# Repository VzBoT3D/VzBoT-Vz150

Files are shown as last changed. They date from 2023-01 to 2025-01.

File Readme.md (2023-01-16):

# VzBoT  <a href='https://ko-fi.com/vez3d' target='_blank'>Buy Me a Coffee at ko-fi.com</a> 

Discord Invite (https://discord.gg/KWZWvCMxCq)

The Vz-150 is a smaller sized VzBoT with a bed print size of 150 x 150 x 125 mm and an optional AWD setup, for which we named the Kinematics "QuadXY" 

The AWD version is still very experimental but is proving to be great for high speed printing without loss of quality!

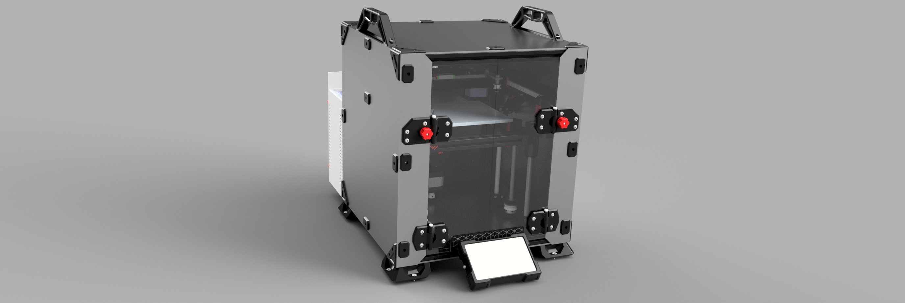
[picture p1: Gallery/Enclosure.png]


This project is licensed as


https://creativecommons.org/licenses/by-nc/4.0/

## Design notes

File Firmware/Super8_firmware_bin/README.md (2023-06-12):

## Pre-compile firmware for the 3 different Super8 versions: 

Instructions:

1. Check your board to make sure you are flashing the right versions. There are 3 versions for now.
    - Super8 standard v1.x (STM32F407 @ 168mhz)
    - Super8 Pro (first edition with STM32H743 chip @ 480mhz)
    - Super8 Pro (latest edition with STM32H723 chip @ 525mhz)

2. Download the according firmware file and rename it to firmware.bin
3. Plate the firmware.bin file on the Super8 Pro SDCARD
4. power on 



Super8 V1.x Standard (STM32F407 @ 168mhz):
 

Super8 Pro (first edition with STM32H743 chip @ 480mhz):
 

Super8 Pro (latest edition with STM32H723 chip @ 525mhz):


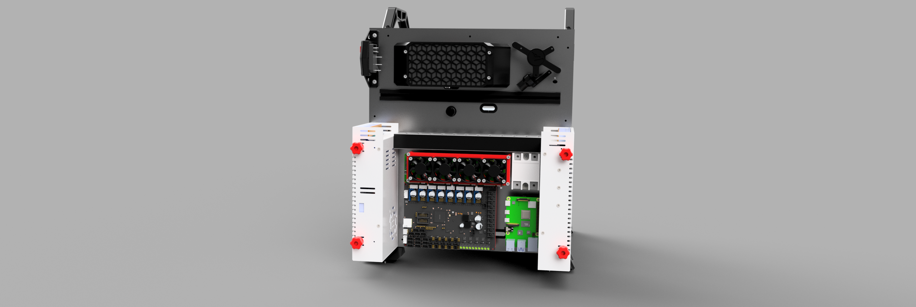
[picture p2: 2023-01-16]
Gallery/Electronics.png

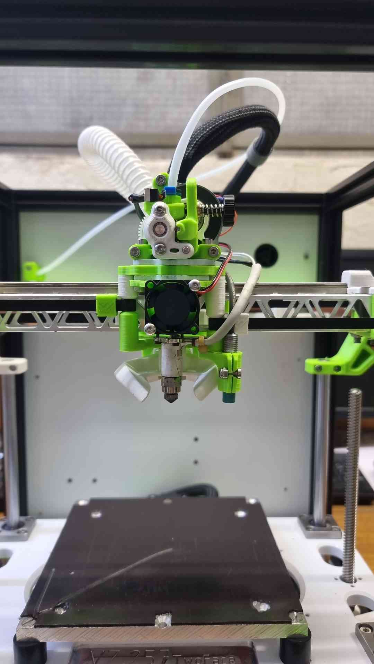
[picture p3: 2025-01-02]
Gallery/IMG-20240227-WA0013.jpg

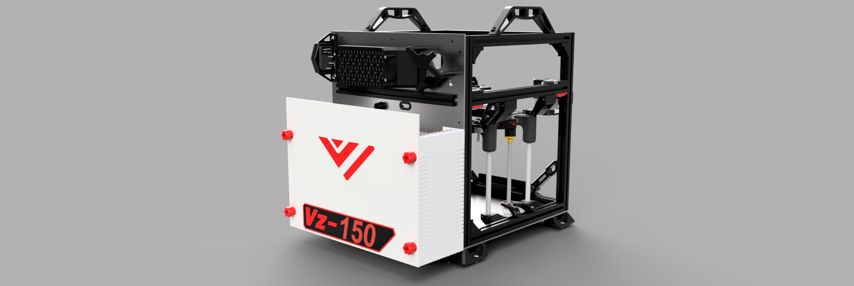
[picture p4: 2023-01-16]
Gallery/Backside.png

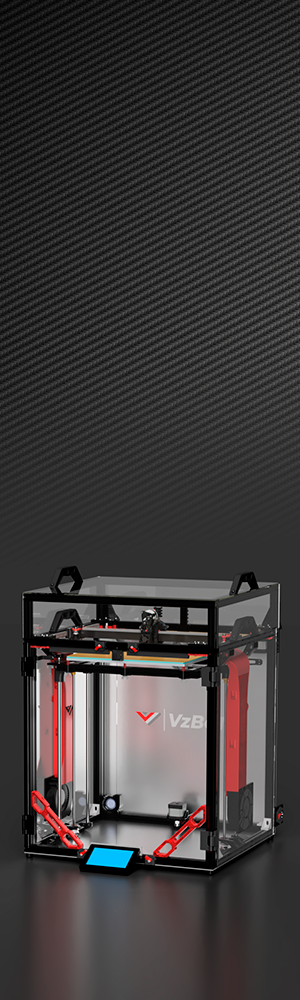
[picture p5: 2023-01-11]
mainsail theme/Theme1/sidebar-background.png

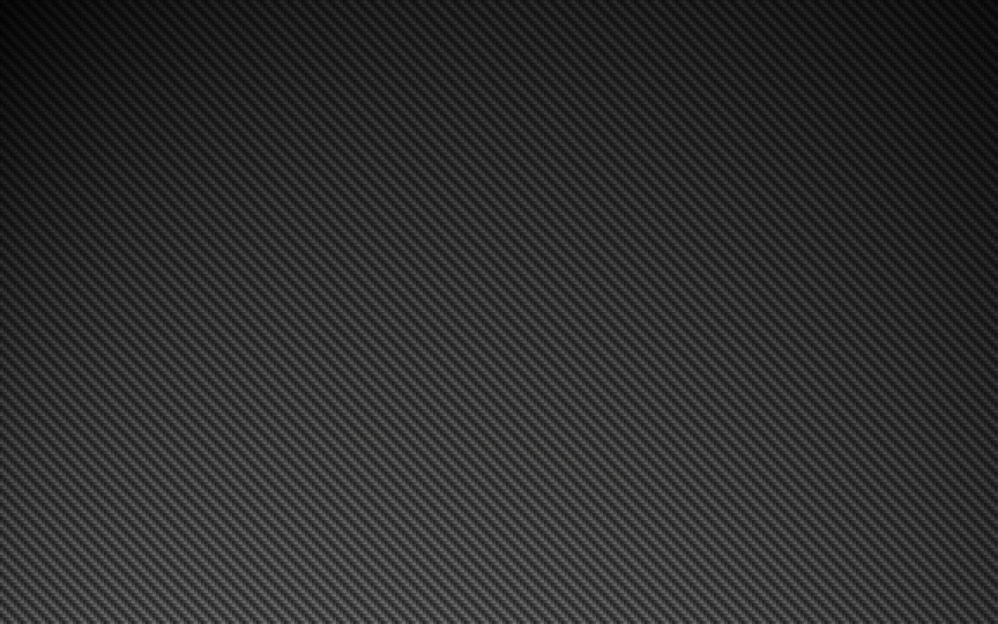
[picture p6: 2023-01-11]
mainsail theme/Theme1/main-background.png

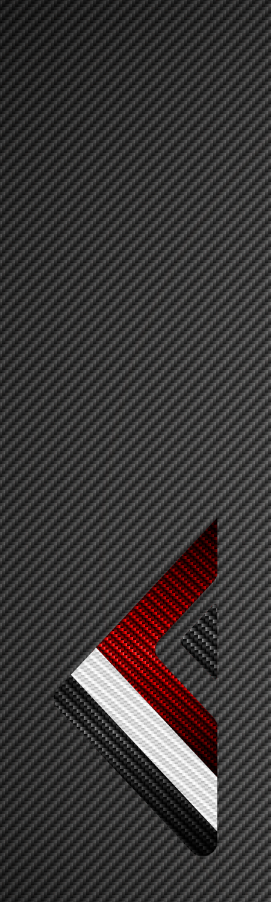
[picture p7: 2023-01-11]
mainsail theme/Theme2/sidebar-background.png

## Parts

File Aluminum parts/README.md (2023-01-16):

# Aluminium parts 

## As available at https://f3d-racing-fdm.myshopify.com/collections/vzbot-vz235

Download the full manual, which includes BOM & print list for all aluminum goodness, above or download the per product manual

Vz150 uses the Aluminium AWD and 2WD mounts from the Vz235. this also includes the Front motor mounts and aluminium Y mounts.

For the Aluminium Y mounts a extra adapter piece is needed found here: [adapter](https://github.com/VzBoT3D/VzBoT-Vz150/tree/main/Aluminum%20parts/Y%20gantry%20adapter)

AWD gantry4

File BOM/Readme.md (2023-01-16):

Work in Progress. Bolts section not fully up to date.

[BOM](https://docs.google.com/spreadsheets/d/1rttVg8Ff3fgsPedlMMFiKo6rYP4tSjWZuqir-3zcSh8/edit?usp=sharing)

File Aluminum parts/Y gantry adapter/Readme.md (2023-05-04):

The adapters can be bought here [MGN9C Adapter](https://s.click.aliexpress.com/e/_DBB861L)

Or you can make them yourself with the provided file.
This part is best when made in aluminium.

BOM:

4x M3x8 Socket Head.                    For mounting the Aluminium Y parts to the adapter.
4x M3x4 Button Head or Ultra Flat head. For mounting the Adapter to the MGN9C carriage.

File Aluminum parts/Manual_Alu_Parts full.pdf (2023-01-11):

## About

This manual is intended for the aluminum parts for VZ235 as sold by F3D-Racing and Mellow. The aluminum parts are interchangeable with the printed parts, some additional hardware is required when purchasing the motor mounts and idler mounts. Furthermore some printed parts are required in order to mount your new sexy parts!

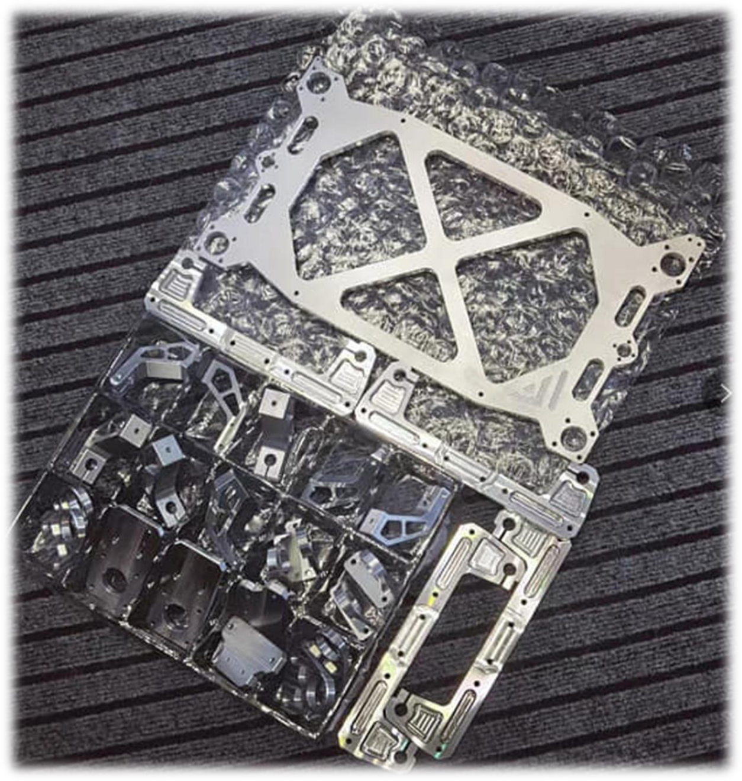
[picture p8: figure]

*Disclaimer: VzBoT is an opensource passion project, this manual is not definitive, and we try to make it as polished as possible. Fortunately, we all make errors so use common sense when following this guide.

## Print settings:

We recommend printing all parts in ABS, ASA or similar material to be able to withstand the high heat environment in the printer enclosure.

Print settings should always be tuned for your own material and tested for decent strength and layer adhesion.

We recommend the following settings:

For non-moving parts:

Layer height: 0.2mm

Layer with: 0.4 to 0.6 mm

Number of walls: 4

Infill percentage: 40 to 50 %

Top/bottom layers: 5

For moving parts:

Layer height: 0.2mm

Layer with: 0.4 to 0.6 mm

Number of walls: 4

Infill percentage: 30 to 40 % depending on your material

Top/bottom layers: 5

## 1. Gantry

Overview:

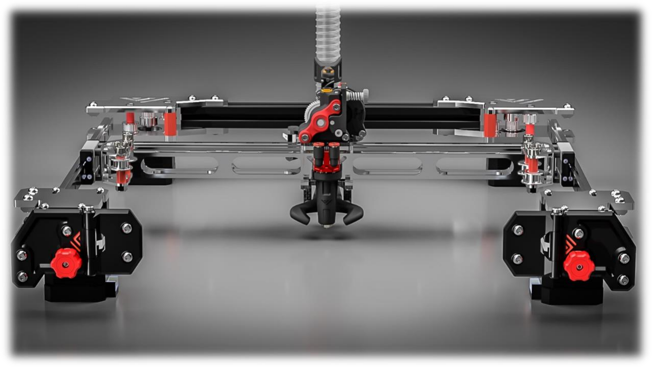
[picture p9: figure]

The Gantry is configurable for an AWD version and a 2WD version. The only difference between the two configurations is the rear idler mounts. On AWD they have an additional Nema 17 integrated in the design.

1.1 Motor mounts + integrated hinges

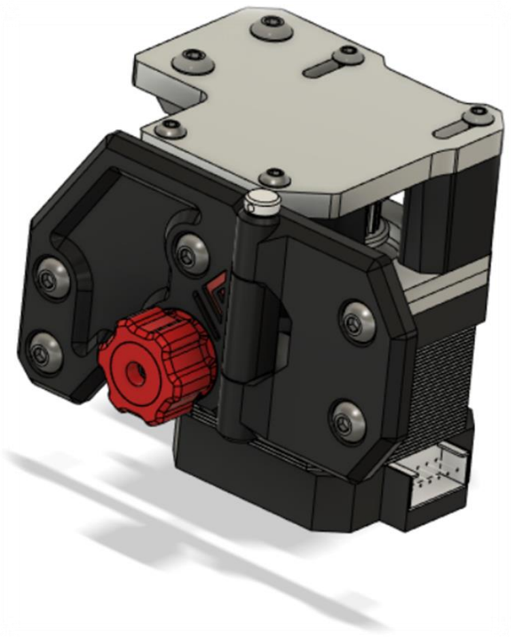
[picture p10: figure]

Bom:
Material | Quantity | Notes
Nema 17 | 2
20T GT2 Pulley | 2
8mm M4 countersunk | 2
30mm M4 set screw | 2
40mm M4 Socket head | 4
M4 nut | 10 | (also, for hinges)
M3 nut | 8
M3 6mm | 4
M3 12mm | 4
M3 10mm countersunk | 4
M4 12mm | 8
M4 10mm | 8
M4 T-nut | 8
M3 35mm | 4
4mm ID washer | 2

STL files:
File name | Amount to print
Printed standoff | Left + Right
Printed standoff 2 | Left + Right
Printed standoff_motor anchor | Left + Right
Tensioner knob | 2
Cap | 2
Integrated hinge | 2
Front plate alu motormount | Left + Right

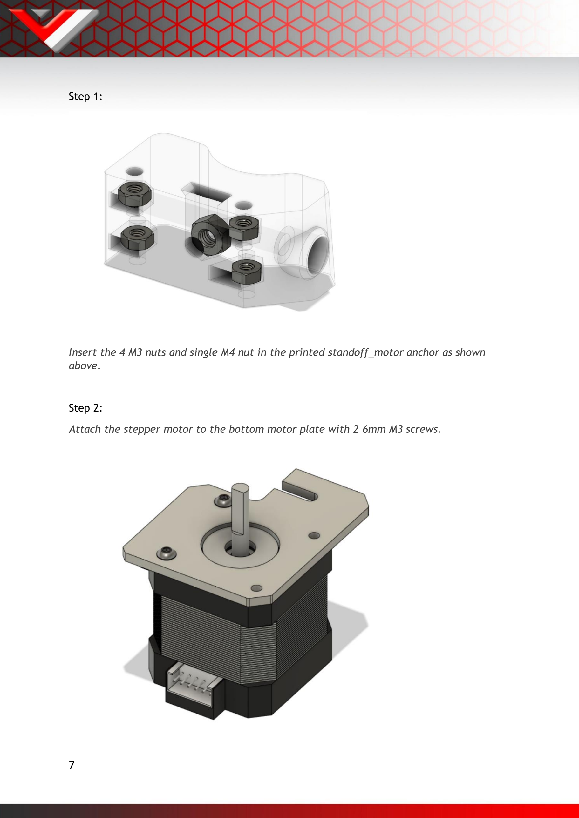
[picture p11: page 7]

Step 1:

Insert the 4 M3 nuts and single M4 nut in the printed standoff_motor anchor as shown above.

Step 2:

Attach the stepper motor to the bottom motor plate with 2 6mm M3 screws.

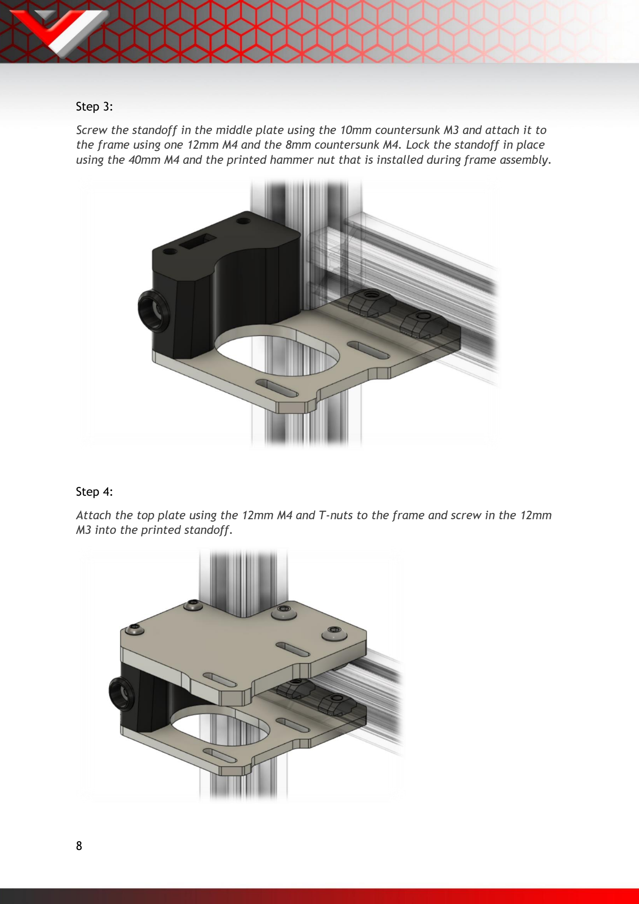
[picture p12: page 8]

Step 3:

Screw the standoff in the middle plate using the 10mm countersunk M3 and attach it to the frame using one 12mm M4 and the 8mm countersunk M4. Lock the standoff in place using the 40mm M4 and the printed hammer nut that is installed during frame assembly.

Step 4:

Attach the top plate using the 12mm M4 and T-nuts to the frame and screw in the 12mm M3 into the printed standoff.

Step 5:

Insert the final standoffs and insert the 35mm M3, slide in the motor with its plate and tighten the M3 screws finger tight.

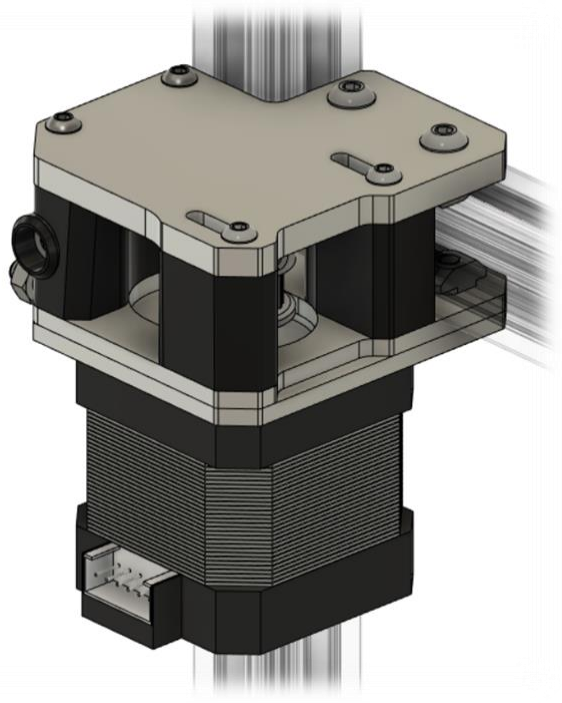
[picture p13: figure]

Step 6:

Screw in the M4 set screw into the bottom tensioner, the M4 nut should be pressed into the tensioning knob. The tensioner plate can be installed when the enclosure panels are on the printer.

1.2 Secondary motor mounts/Idlers (AWD)

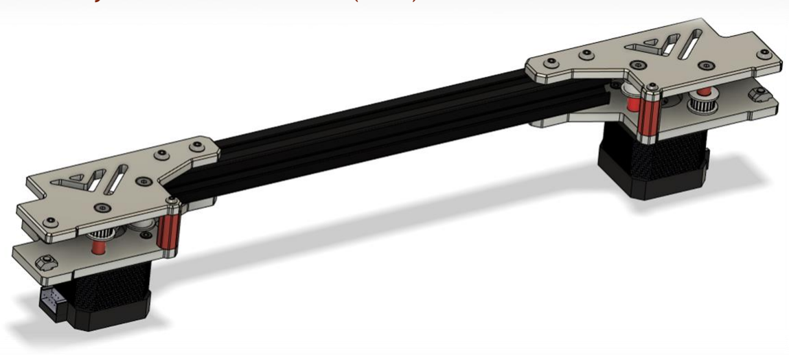
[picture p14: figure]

Bom:
Material | Quantity | Notes
M3 35mm | 2
M3 nut | 2
M3 6mm | 6
M4 10mm | 12
M4 T-nut | 12 | +3 when mounting the extrusion to the rear panel
Shoulder bolt 5mmx20mm [M3] | 4 | M3 threading with 6mm of threaded length, if longer grind down the ends https://nl.aliexpress.com/item/1005003611471729.html
M4 nut | 2
GT2 Toothed idler | 2 | Low profile required, as available at Mellow & F3D
Gt2 Smooth idler | 2 | Low profile required, as available at Mellow & F3D
GT2 motor pulley | 2
260mm 2020 Extrusion | 1
M4 8mm | 3 | Optional but recommended, used to secure the rear extrusion to the rear aluminum panel

STL files:
File name | Amount to print
Spacer long | 4
Spacer short bottom | 2
Spacer short top | 2
Spacer M3 corner | 2

Step 1:

Mount the motor to the bottom plate with the M3 screws

Step 2:

Mount the bottom assembly (left & right) to the frame with the rear extrusion

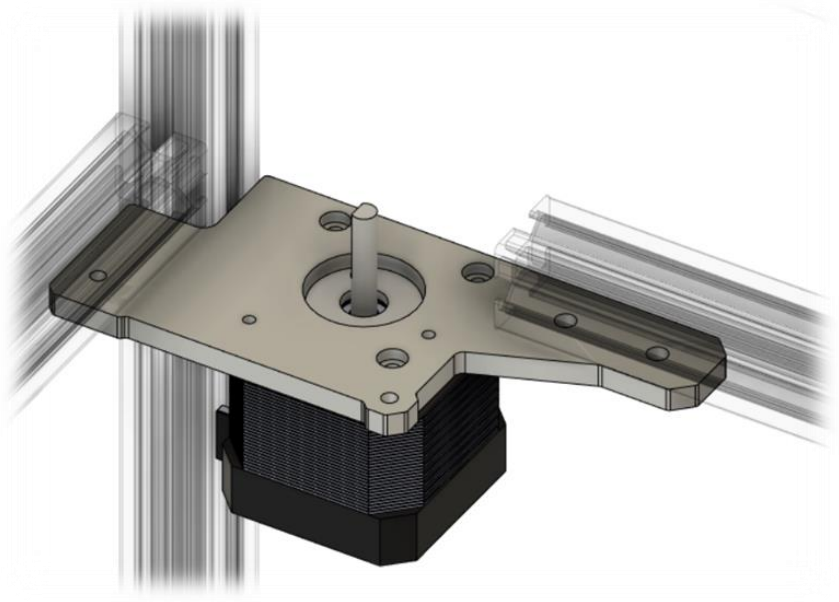
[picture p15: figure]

Step 3:

Mount the pulleys with their respective spacers and hardware like shown below. Mind that the bottom spacer for the toothed idler pulley has a smaller inside diameter then the top one for the smooth idler.

*when getting the top plate in position with all hardware it is recommended to either have the printed parts printed with some excess first layer squish or put some thicker grease between the last spacer and the shoulder bolt to keep the assembly together before mounting


Step 4:

Secure the top plate

## 2.1 Lower rod & leadscrew bracket

Bom:

Material | Quantity | Notes
10mm M4 | 4
12mm M4 | 16
608-2RS (skateboard) bearing | 4
GT2 40T 8mm bore Pulley | 2
300mm 10mm rods | 4

Belt GT2 closed, length 860-870 mm

STL files:

File name | Amount to print
Z assembly alignment tool (either EVA/VZprinthead) | 1

Step 1:
Mount the top bracket with the 12mm M4 hardware to the frame loosely. Then mount the sliding rods with 12mm M4 screws and align the assembly to the frame using the printed “Z assembly alignment tool”. Be sure to secure all hardware. Be sure to either insert 2 T-nuts underneath the center two holes for the top leadscrew bracket or immediately mount the top bracket.


Step 2:
Mount the lower leadscrew bracket, using 2x 10mm M4 screws, loosely to the frame approximately in the correct position relative to the top bracket.


Step 3:
Mount the top leadscrew bracket to the assembly using 12mm M4 screws (skip when done in step one). Insert the pulley with the closed belt and insert the leadscrew. Then tighten the grub screws on the pulley. Lastly while making sure the leadscrew is perfectly straight up tighten the screws on the upper and lower leadscrew brackets. This can be checked by measuring the distance on both sides between the leadscrew (top position) and the 10mm Rods.


Step 4:
Repeat steps 1 through 3 for the other side.

## 2.2 Bed assembly


Bom:

Material | Quantity | Notes
M4 8mm | 16
M3 8mm | 16
M3 50mm | 4 | Countersunk for the bed
M3 nuts | 12
LMK10LUU | 4
Oldham coupler | 2 | Optional but highly advised
Leadscrew nut | 2

STL files:

File name | Amount to print
Bed level adjustment knobs | 4
Oldham couplers | optional


Step 1:
Mount the LMK10LUU using the M4 hardware to the bed frame. Then mount the Oldham couplers with the leadscrew nuts together with M3 hardware and mount that assembly to the bed frame using M3 hardware
Step 2:
Place the bed assembly in the rods and leadscrew.

Step 3:
Mount the bed plate to the bed frame using the 50mm countersunk M3 screws. When using a cast aluminum bed make sure it is well prepped before mounting. It is recommended to always be safe and inform yourself properly on how to apply a AC silicon heating pad.


## 2.3 Top rod mounts


Bom:

Material | Quantity | Notes
M4 10mm | 4
M4 20mm | 4
M4 T-nut | 4

Step 1:
Mount the 10mm M4 screws and T-nuts to all top rod mounts and loosely turn in the 20mm M4 screws in the clamping mechanism.


Step 2:
Mount all top rod mounts to the rod first. Make sure the rod mount with the extra hole (for the Z limit switch) is in the back right of the printer like shown below. Finally tighten the rod holders to the frame with the pre-inserted M4 hardware.


Step 3:
After installing check the movement of the bed assembly by turning the leadscrews. This should operate smoothly. If not, place the bed assembly in the top most position, untighten all top rod holders and retighten to align the rods.

## 2.4 Single z motor bracket

Bom:

Material | Quantity | Notes
M3 10mm | 4
M4 10mm | 4
M4 T-nut | 2
20t GT2 | 1
NEMA 17 stepper | 1

Step 1:
Mount the bracket shown below to the frame using the 10mm M4 screws and T-nuts. Make sure it is nicely centered in the middle of the frame.


Step 2:
Mount the stepper motor to the top bracket using the 10mm M3 screws. Attach the motor pulley like shown below.


Step 3:
Mount the previous assembly to the bracket on the frame using 10mm M4 screws.


Step 4:
With the motor in the furthest position, loop the belt around the motor pulley and tighten the belt. Be sure to check if the belt is horizontally parallel to the frame for smoothest operation.

## 2.5 Z switch & bed chain

Bom:

Material | Quantity | Notes
M3 10mm | 4
M3 8mm | 1
M2 10mm | 2
M3 40mm | 1
M3 nut | 3
Microswitch | 1

STL files:

File name | Amount to print
Printed z switch adapter | 1
Z-chain mount | 1
Step 1:
Mount the printed chain mount to the bed frame using the 10mm M3 screws. Then mount the cable chain using 10mm M3 screws and nuts like shown below.


Step 2:
Mount the microswitch to the printed adapter using M2 screws. Then mount the assembly to the top rod holder using the 8mm M3. Finally screw in the 50mm M3 screw and nut like shown below. After setting the correct Z-height using the adjustment screw use the M3 nut to lock the screw in place in order to make sure the screw doesn’t drift off position.


Designed and developed by:

The VzBot Team

https://discord.gg/qmMeD6Vt3W

https://www.facebook.com/groups/4098868770205560/

https://github.com/VzBoT3D

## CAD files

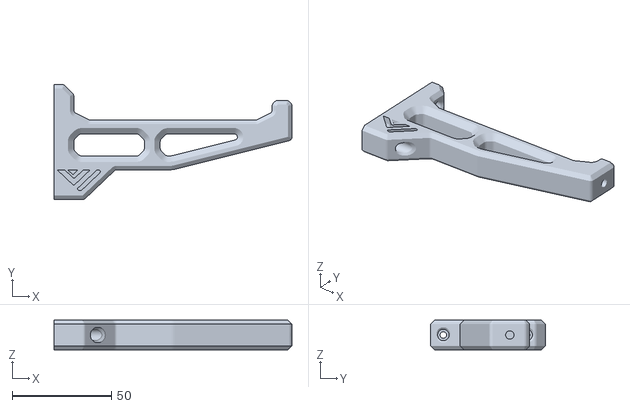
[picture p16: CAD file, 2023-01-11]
Assemblies & STL/Spool holder/main body.stl
120.0 x 58.0 x 15.0

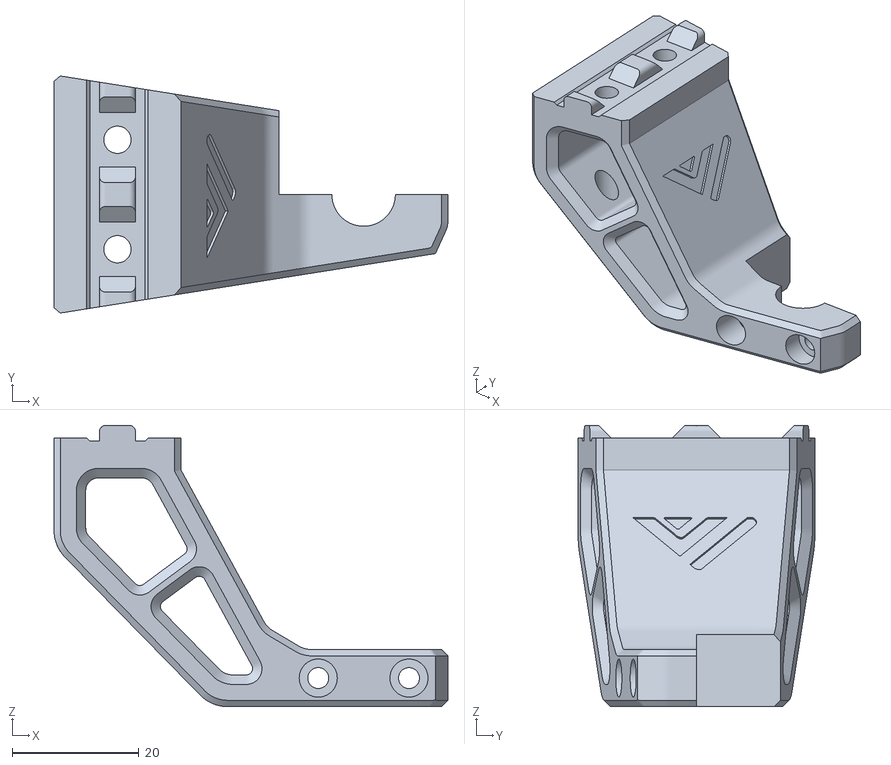
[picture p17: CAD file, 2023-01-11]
Assemblies & STL/Z-Assembly/parts to print 2 & 4 times/upper rod mount main.stl
62.1 x 37.4 x 44.3

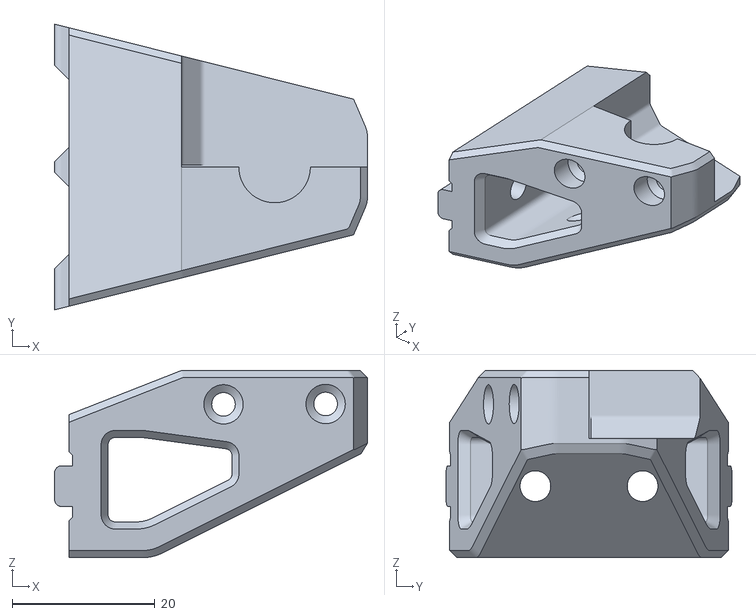
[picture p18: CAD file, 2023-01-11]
Assemblies & STL/Z-Assembly/parts to print 2 & 4 times/lower rod mount main.stl
43.8 x 40.0 x 26.2

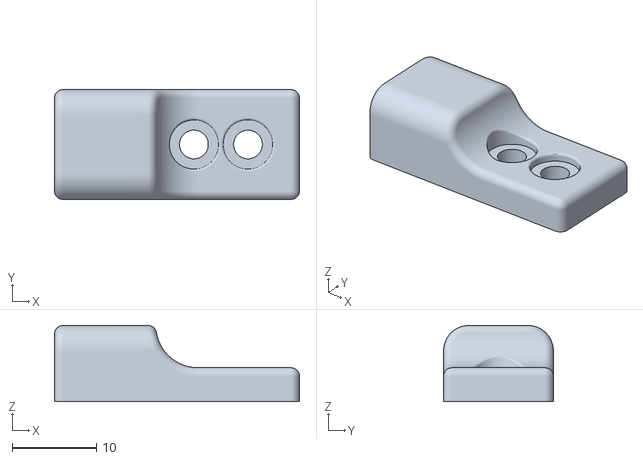
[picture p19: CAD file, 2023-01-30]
Aluminum parts/Y gantry adapter/X_Stopblock.stl
29.0 x 13.0 x 9.00

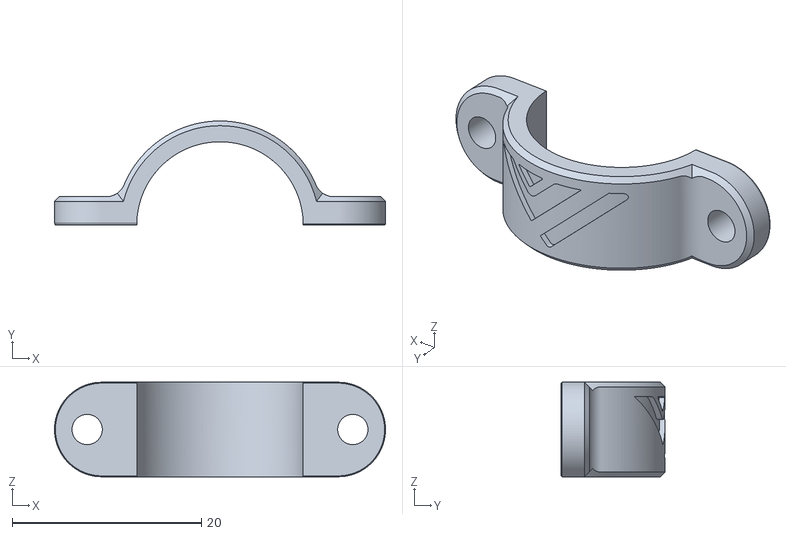
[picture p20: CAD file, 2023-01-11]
Assemblies & STL/CPAP turbo cooling system/STLs/c-clamp.stl
35.0 x 11.0 x 10.0

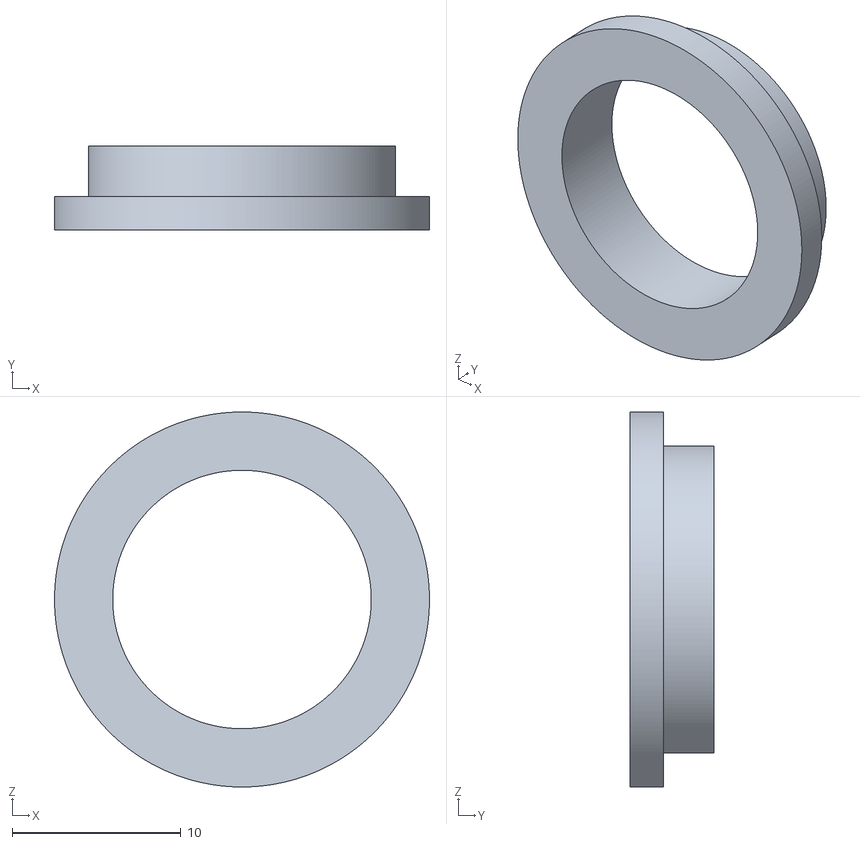
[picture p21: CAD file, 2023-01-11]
Assemblies & STL/CPAP turbo cooling system/STLs/CPAP back panel tube mount/optinal cap (need 18.2mm hole.stl
22.2 x 5.00 x 22.2

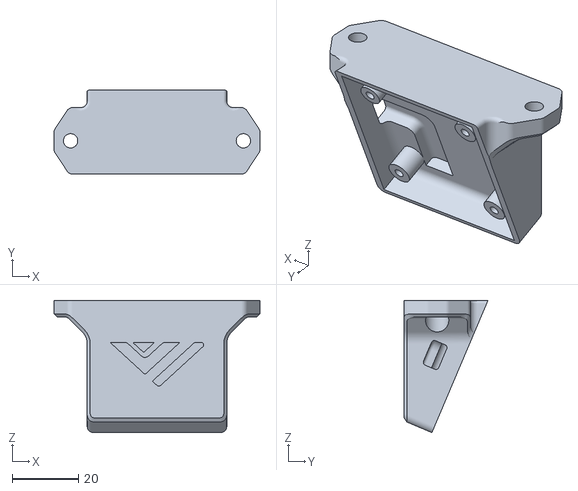
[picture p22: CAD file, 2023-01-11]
Assemblies & STL/Electronics/ArducamMount/enclosure.stl
62.0 x 25.3 x 39.8

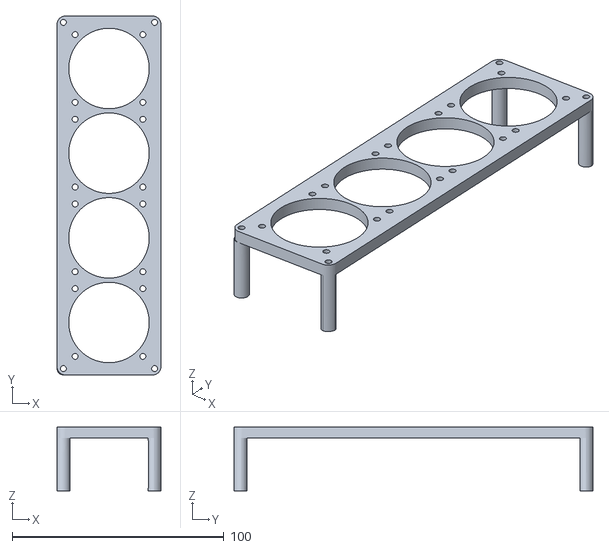
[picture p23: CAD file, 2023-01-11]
Assemblies & STL/Electronics/Fly Super8/FlySuper8 fan cover.stl
49.1 x 169.6 x 30.0

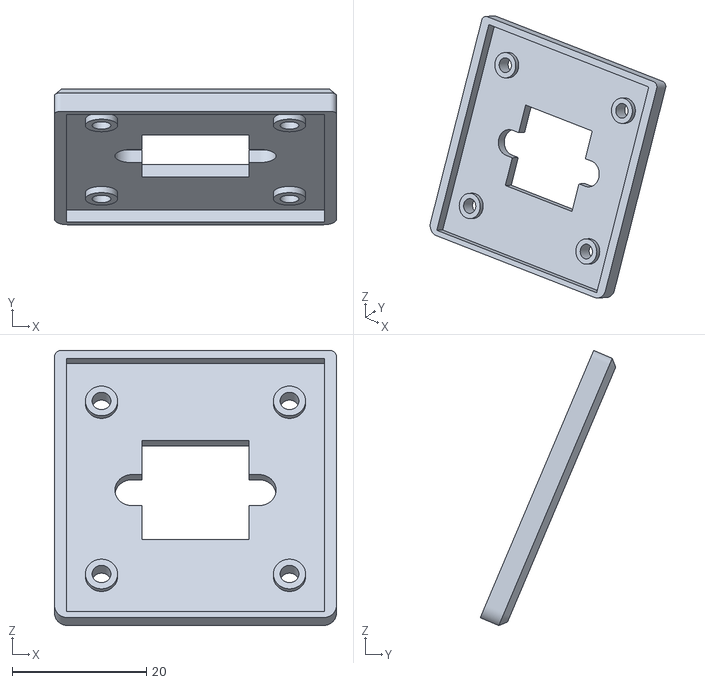
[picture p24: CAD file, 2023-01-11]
Assemblies & STL/Electronics/HBVCAM-F20216HD/cover.stl
42.0 x 20.2 x 41.0

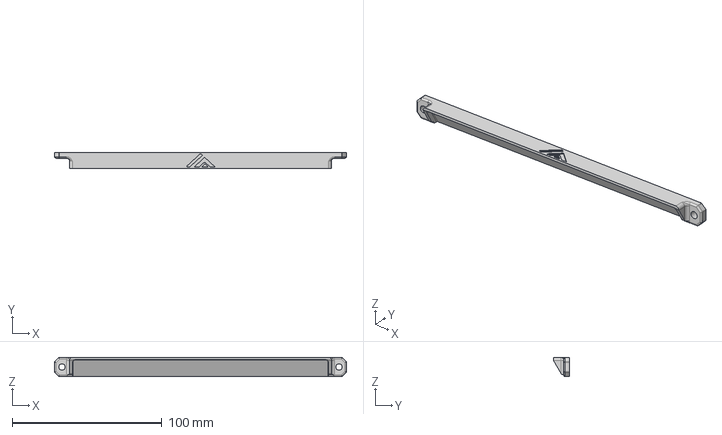
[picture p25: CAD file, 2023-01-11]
Assemblies & STL/Electronics/Optional Front LED/Led mount.step
195.0 x 11.0 x 12.8 mm

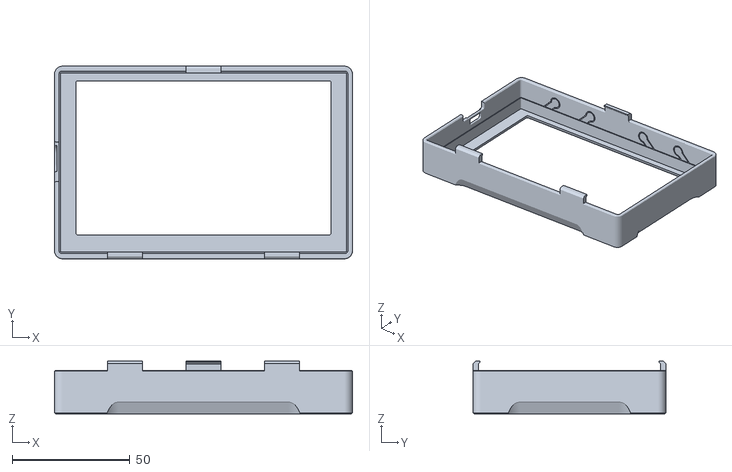
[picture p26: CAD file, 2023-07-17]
Assemblies & STL/Electronics/Screen Mount/Mellow-Fly Version/Front cover.stl
126.7 x 81.9 x 22.5

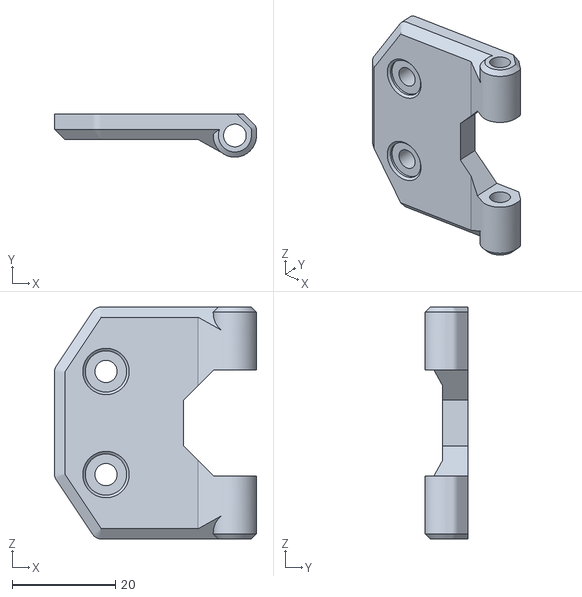
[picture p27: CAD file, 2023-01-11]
Assemblies & STL/Enclosure/Doors/hinges [lower]/door side.stl
39.2 x 8.40 x 45.0

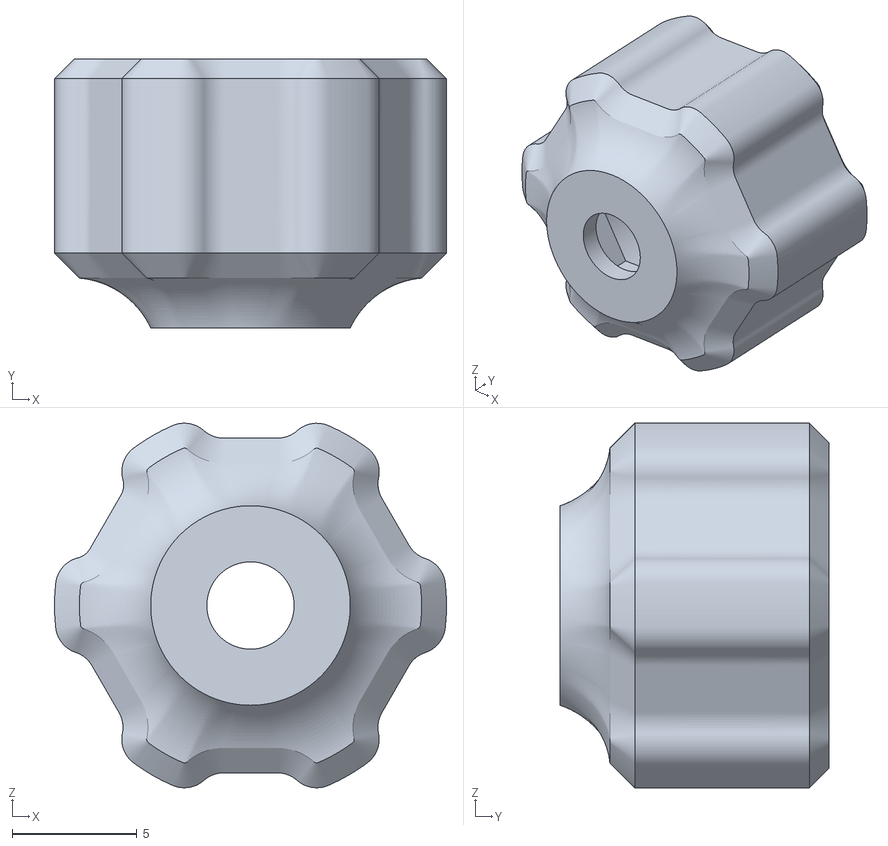
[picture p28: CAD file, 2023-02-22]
Assemblies & STL/Enclosure/Doors/Knob_x2.stl
15.7 x 10.8 x 14.6

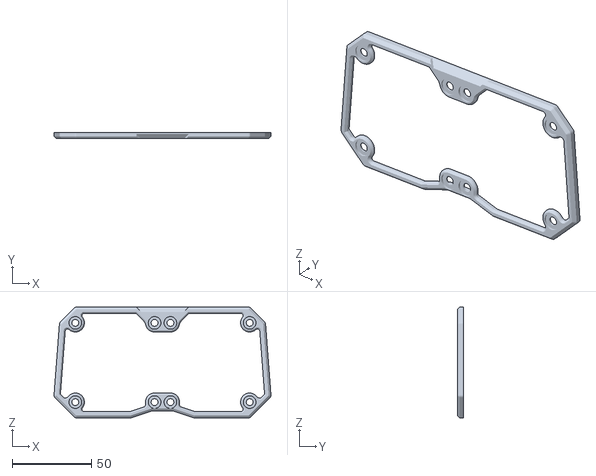
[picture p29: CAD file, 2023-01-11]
Assemblies & STL/Enclosure/Fume extractor/fume extractor/fan guard.stl
136.9 x 4.00 x 70.0

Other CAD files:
Assemblies & STL/Enclosure/Misc/misc/Led strip holder [print in vase mode].stl
Assemblies & STL/Enclosure/Panel Trim Pieces/panel middle piece.stl
Assemblies & STL/Enclosure/TPU Grommets (optional)/grommet slotted.stl
Assemblies & STL/EVA Vz150/EVA 2.3 Compatible/Eva 2.3 compatible/bottom_mgn12_short_duct.stl
Aluminum parts/Y gantry adapter/Y_Stopblock.stl
Assemblies & STL/CPAP turbo cooling system/STLs/CPAP back panel tube mount/Lower CPAP body.stl
Assemblies & STL/CPAP turbo cooling system/STLs/CPAP back panel tube mount/Upper Cpap body.stl
Assemblies & STL/CPAP turbo cooling system/STLs/CPAP fan mount.stl
Assemblies & STL/CPAP turbo cooling system/STLs/CPAP fan outlet adapter.stl
Assemblies & STL/CPAP turbo cooling system/STLs/upper duct mount.stl
Assemblies & STL/EVA Vz150/EVA 2.3 Compatible/Eva 2.3 compatible/Duct v2.1 Straight.stl
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

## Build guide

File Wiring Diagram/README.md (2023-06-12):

# PLEASE NOTE: IMPORTANT : ALWAYS CONNECT BOTH PSU DC NEGATIVE TOGETHER SO THEY HAVE THE SAME REFERENCE GROUND 
## For 48v stepstick drivers: The super 8 has 2 seperate bank of drivers. 0-2 and 3 to 7. If you want to run your Z and and E on 24v and XY on 48v, you have to use 24V on port 0-2 and place your 48v on port 3-7 for step stick driver.
## If you use the external 5160HV Pro from Mellow, then you can use the port that you want and feed 24v on both driver banks and supply 48v ONLY to the external drivers directly. 
## The new version of the External 5160HV Pro has a direct 12v Fan connection on the driver board, so no need to use a port on the Super8 for that. Connect the fans directly to the driver boards

# Useful links:
- Super8 and Super8 Pro Documation: https://teamgloomy.github.io/fly_super8_general.html
- Super8 Std Klipper info: https://mellow.klipper.cn/#/board/fly_super8/
- Super8 Pro Klipper info: https://mellow.klipper.cn/#/board/fly_super8_pro/

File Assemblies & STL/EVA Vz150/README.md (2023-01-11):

## Due to the slightly different belt routing of the VZ330,VZ235 and VZ150 the standard EVA platform can't be used. VZ235, VZ330 and VZ150  use their own modified version

all printed parts have been put into folders seperated by supported platform. 
to find all parts needed one will need to download all parts in the folder fitting their respective build options

Step 1: Choose to use the fan ducting for EVA 2.3 or 2.4

Step 2: choose the hotend 

Step 3: choose extruder combo (the standard loadout is the hextrudort version which will be found in universal parts folder as it will fit both 2.3 and 2.4)

Step 4: print and have fun!

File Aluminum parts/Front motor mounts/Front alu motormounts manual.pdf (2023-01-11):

3.1 Motor mounts + integrated hinges

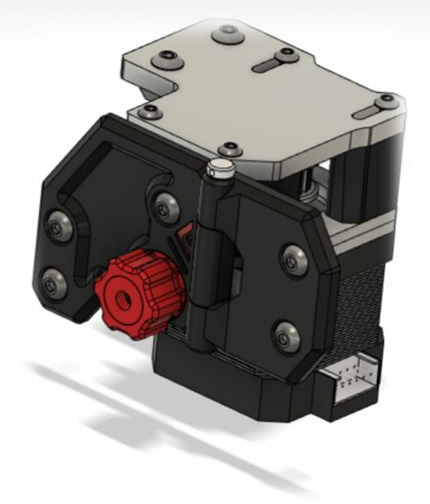
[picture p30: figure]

Bom:
Material | Quantity | Notes
Nema 17 | 2
20T GT2 Pulley | 2
8mm M4 countersunk | 2
30mm M4 set screw | 2
40mm M4 Socket head | 4
M4 nut | 10 | (also, for hinges)
M3 nut | 8
M3 6mm | 4
M3 12mm | 4
M3 10mm countersunk | 4
M4 12mm | 8
M4 10mm | 8
M4 T-nut | 8
M3 35mm | 4
4mm ID washer | 2

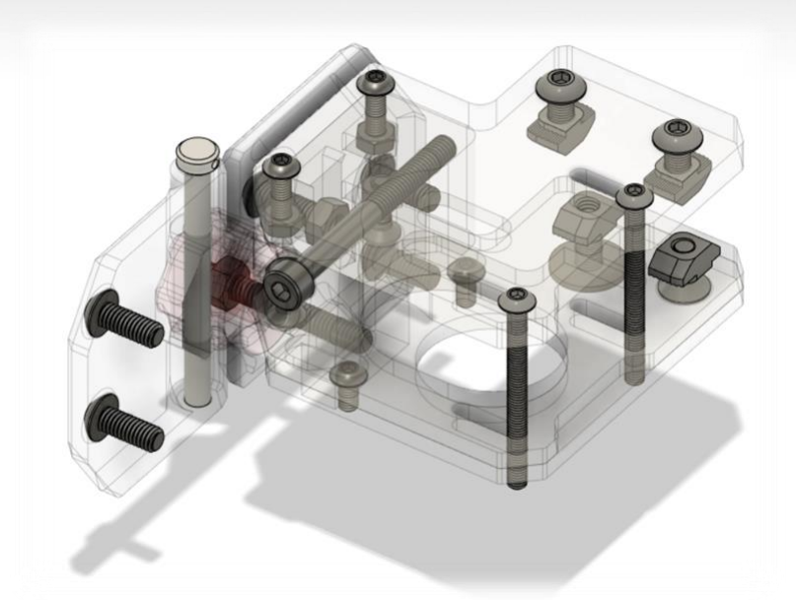
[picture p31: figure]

STL files:
File name | Amount to print
Printed standoff | Left + Right
Printed standoff 2 | Left + Right
Printed standoff_motor anchor | Left + Right
Tensioner knob | 2
Cap | 2
Integrated hinge | 2
Front plate alu motormount | Left + Right

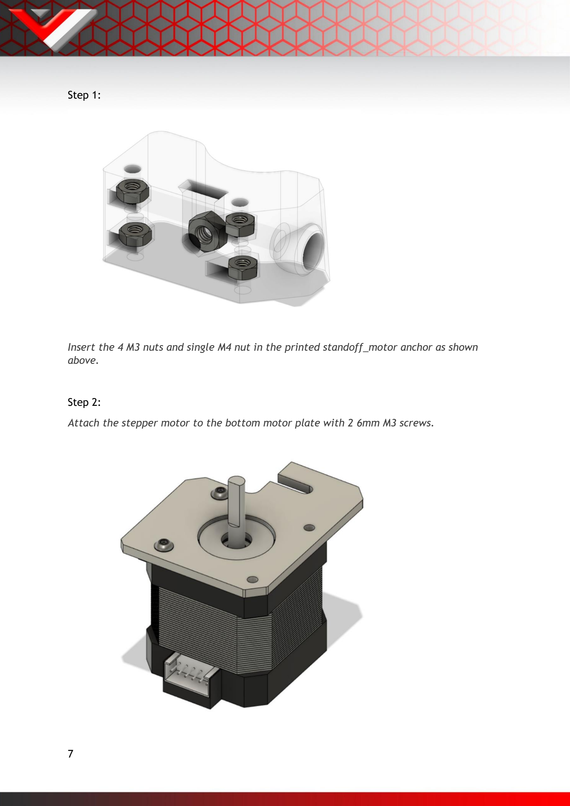
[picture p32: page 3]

Step 1:

Insert the 4 M3 nuts and single M4 nut in the printed standoff_motor anchor as shown above.

Step 2:

Attach the stepper motor to the bottom motor plate with 2 6mm M3 screws.

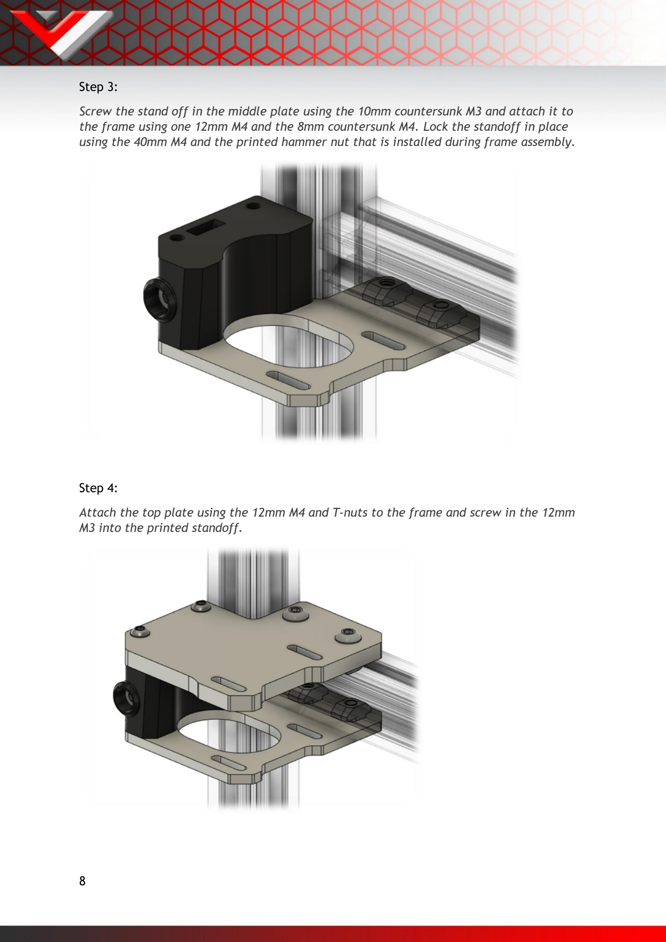
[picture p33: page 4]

Step 3:

Screw the stand off in the middle plate using the 10mm countersunk M3 and attach it to the frame using one 12mm M4 and the 8mm countersunk M4. Lock the standoff in place using the 40mm M4 and the printed hammer nut that is installed during frame assembly.

Step 4:

Attach the top plate using the 12mm M4 and T-nuts to the frame and screw in the 12mm M3 into the printed standoff.

Step 5:

Insert the final standoffs and insert the 35mm M3, slide in the motor with it’s plate and tighten the M3 screws finger tight.

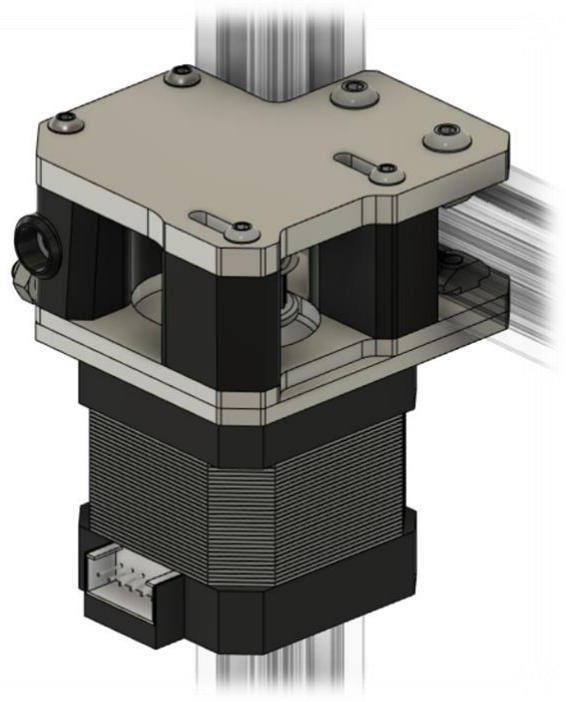
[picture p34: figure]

Step 6:

Screw in the M4 set screw into the bottom tensioner, the M4 nut should be pressed into the tensioning knob. The tensioner plate can be installed when the enclosure panels are on the printer.

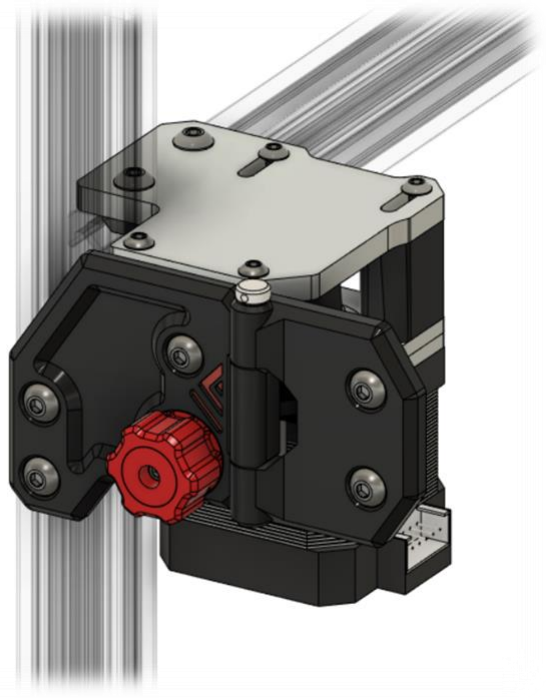
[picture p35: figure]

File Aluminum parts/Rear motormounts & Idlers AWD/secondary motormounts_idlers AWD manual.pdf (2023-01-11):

1.2 Secondary motor mounts/Idlers (AWD)


Bom:
Material | Quantity | Notes
M3 35mm | 2
M3 nut | 2
M3 6mm | 6
M4 10mm | 12
M4 T-nut | 12 | +3 when mounting the extrusion to the rear panel
Shoulder bolt 5mmx20mm [M3] | 4 | M3 threading with 6mm of threaded length, if longer grind down the ends https://nl.aliexpress.com/item/1005003611471729.html
M4 nut | 2
GT2 Toothed idler | 2 | Low profile required, as available at Mellow & F3D
Gt2 Smooth idler | 2 | Low profile required, as available at Mellow & F3D
GT2 motor pulley | 2
260mm 2020 Extrusion | 1
M4 8mm | 3 | Optional but recommended, used to secure the rear extrusion to the rear aluminum panel

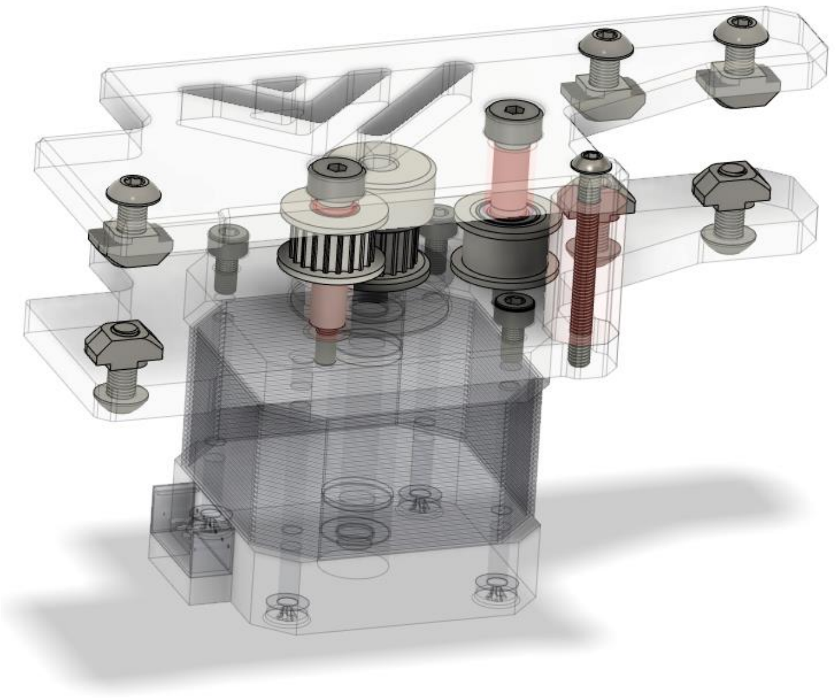
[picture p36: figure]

STL files:
File name | Amount to print
Spacer long | 4
Spacer short bottom | 2
Spacer short top | 2
Spacer M3 corner | 2

Step 1:

Mount the motor to the bottom plate with the M3 screws

Step 2:

Mount the bottom assembly (left & right) to the frame with the rear extrusion


Step 3:

Mount the pulleys with their respective spacers and hardware like shown below. Mind that the bottom spacer for the toothed idler pulley has a smaller inside diameter then the top one for the smooth idler.

*when getting the top plate in position with all hardware it is recommended to either have the printed parts printed with some excess first layer squish or put some thicker grease between the last spacer and the shoulder bolt to keep the assembly together before mounting

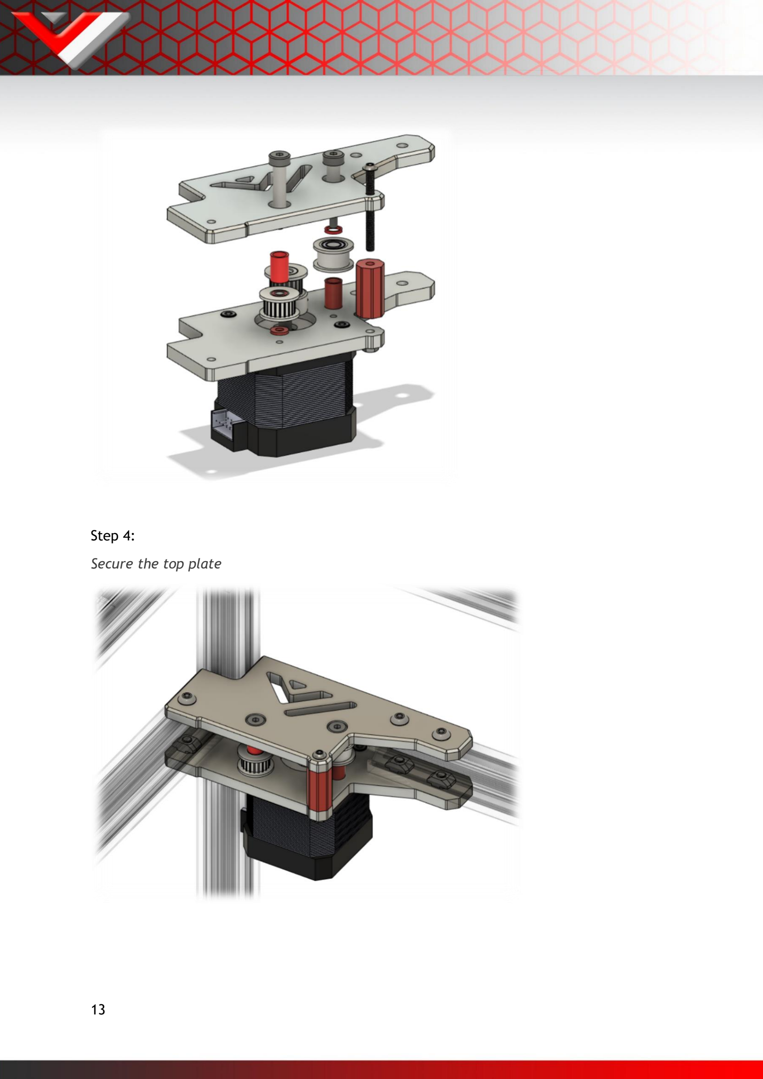
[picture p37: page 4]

Step 4:

Secure the top plate

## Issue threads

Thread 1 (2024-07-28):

5mm bolt in 3mm hole

NikopolCZ, 2024-07-28:
On both back pulley mounts is a mistake in design. There is a 5mm bolt goin through 3mm hole in a bearing.
Also an idea. You can replace back motors without disasambling everything, if you make lower back pulley motor mount holes also in upper mount.

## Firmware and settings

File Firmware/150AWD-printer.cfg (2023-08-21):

### For Fly Super 8 V1.3 ####
### And Mellow Kit  ####
### For Fly Super pro 8, the SPI bus is spi1A
### For Fly Super 8 V1.3, the SPI bus is spi3

[include mainsail.cfg]
[include timelapse.cfg]
[include Exclude_Object.cfg]
[include Start_Stop.cfg]
[include Macro.cfg]
[include Speed.cfg]
[display_status]
[exclude_object]
[virtual_sdcard]
path: ~/gcode_files
[pause_resume]
recover_velocity: 350


##### VzBoT############
#######################

[printer]
kinematics: corexy
max_velocity: 2500
max_accel: 10000
#max_accel_to_decel: 5000
max_z_velocity: 20
max_z_accel: 1500
square_corner_velocity: 10

########################
########################


[mcu]
serial: /dev/serial/by-id/usb-Klipper_stm32f407xx_3E0023000E47323236333832-if00  # put your own Serial here.
#restart_method: command

[temperature_sensor FLY-Super8]
sensor_type: temperature_mcu

[mcu rpi]
serial: /tmp/klipper_host_mcu

[temperature_sensor raspberry_pi]
sensor_type: temperature_host
min_temp: 10
max_temp: 100

########################
########################

[stepper_x]
##	in M6 position
step_pin: PE0
dir_pin: PG3
enable_pin: !PG4
rotation_distance: 40
microsteps: 16
full_steps_per_rotation: 200  
endstop_pin: PF10            #make sure to set the correct pin here.
position_endstop: 0
position_min: 0
position_max: 150
homing_speed: 50 
homing_retract_dist: 0

[tmc5160 stepper_x] 
#spi_bus: spi3
cs_pin: PG2
#diag_pin: PA8
interpolate: false
run_current: 1.9
sense_resistor: 0.033
spi_software_mosi_pin: PB5
spi_software_miso_pin: PB4
spi_software_sclk_pin: PB3
#driver_SGT: -64 # -64 is most sensitive value, 63 is least sensitive
driver_TBL: 1
driver_TOFF: 3
driver_DISS2G: 1
driver_DISS2VS: 1


[stepper_x1]
##	in M5 position
step_pin: PE1
dir_pin: !PF0
enable_pin: !PC15
rotation_distance: 40
microsteps: 16
full_steps_per_rotation: 200
#endstop_pin: tmc5160_stepper_x:virtual_endstop 

[tmc5160 stepper_x1] 
#spi_bus: spi3
cs_pin: PF1
#diag_pin: PD6
interpolate: false
run_current: 1.9
sense_resistor: 0.033
spi_software_mosi_pin: PB5
spi_software_miso_pin: PB4
spi_software_sclk_pin: PB3
#driver_SGT: -64 # -64 is most sensitive value, 63 is least sensitive
driver_TBL: 1
driver_TOFF: 3
driver_DISS2G: 1
driver_DISS2VS: 1


[stepper_y]
##	in M4 position
step_pin: PE15
dir_pin: !PE11
enable_pin: !PF2
rotation_distance: 40
microsteps: 16
full_steps_per_rotation: 200  
endstop_pin: PC0                 #make sure to set the correct pin here.
position_endstop: -0
position_min: 0
position_max: 150
homing_speed: 50  
homing_retract_dist: 0

[tmc5160 stepper_y] 
#spi_bus: spi3
cs_pin: PE10
#diag_pin: PD7
interpolate: false
run_current: 1.9
sense_resistor: 0.033
spi_software_mosi_pin: PB5
spi_software_miso_pin: PB4
spi_software_sclk_pin: PB3
#driver_SGT: -64 # -64 is most sensitive value, 63 is least sensitive
driver_TBL: 1
driver_TOFF: 3
driver_DISS2G: 1
driver_DISS2VS: 1

[stepper_y1]
##	in M3 position
step_pin: PE14
dir_pin: PE8
enable_pin: !PE9
rotation_distance: 40
microsteps: 16
full_steps_per_rotation: 200
#endstop_pin: tmc5160_stepper_y:virtual_endstop  

[tmc5160 stepper_y1] 
#spi_bus: spi3
cs_pin: PE7
#diag_pin: PG9
interpolate: false
run_current: 1.9
sense_resistor: 0.033
spi_software_mosi_pin: PB5
spi_software_miso_pin: PB4
spi_software_sclk_pin: PB3
#driver_SGT: -64 # -64 is most sensitive value, 63 is least sensitive
driver_TBL: 1
driver_TOFF: 3
driver_DISS2G: 1
driver_DISS2VS: 1

#########################

[stepper_z]
## In M1 position
step_pin: PE3
dir_pin: !PF13
enable_pin: !PF14
microsteps: 32
rotation_distance: 4
endstop_pin:               #make sure to set the correct pin here.
#position_endstop: 0.0
position_max: 120
full_steps_per_rotation: 200
homing_retract_dist: 5.0
homing_positive_dir: false
homing_speed: 5.0
second_homing_speed: 2.5
[tmc2209 stepper_z]
interpolate: false
uart_pin: PF12
run_current: 1.2
stealthchop_threshold: 0

[extruder]
## In M0 position
### Vz-HextrudORT
step_pin: PE2
dir_pin: PC5
enable_pin: !PF11
microsteps: 16
#Alu VZhextrudort Moons 8T
rotation_distance: 22.2
Gear_ratio: 50:8
#Alu VZhextrudort Moons 10T
#rotation_distance: 22 
#gear_ratio: 50:10 
#VZHextrudort LDO 20mm
#rotation_distance: 4.71
nozzle_diameter: 0.5
filament_diameter: 1.750

heater_pin: PB0
sensor_type: PT1000
sensor_pin: PF4

#control: pid
#pid_Kp=28.737 
#pid_Ki=1.935 
#pid_Kd=106.684
min_temp: 0
max_temp: 400
full_steps_per_rotation: 200
max_extrude_only_distance: 1000.0
max_extrude_cross_section: 500
max_extrude_only_velocity: 200
max_extrude_only_accel: 10000
min_extrude_temp: 0
pressure_advance: 0.02
pressure_advance_smooth_time: 0.03

[tmc2209 extruder]
uart_pin: PC4
interpolate: false
run_current: 0.7
sense_resistor: 0.110

########################
########################

[heater_bed]
heater_pin: PE5
sensor_type: Generic 3950
sensor_pin: PC1
#control: pid
#pid_Kp: 66.746
#pid_Ki: 3.504
#pid_Kd: 317.878
min_temp: 0
max_temp: 130


########################
#### FANS ##############
########################

[fan]
##	Print Cooling Fan - PF8
pin: PF8
max_power: 1
cycle_time: 0.002
hardware_pwm: false
shutdown_speed: 0

[heater_fan hotend_fan]
##	Hotend Fan - FAN0 Connector
## in case of a watercooler that is 24V use a Heater Pin like PF7 Heat3 for a larger mosfet that can handle more amps.
pin: PA0
max_power: 1.0
kick_start_time: 0.5
heater: extruder
heater_temp: 50.0

#[fan_generic Exhaust_fan]
##  exhaust fan - In FAN4
#pin: PA15
#max_power: 1
#shutdown_speed: 0
#kick_start_time: 0.1
#off_below: 0.10

#[fan_generic chamber_fan]
###  chamber fan - In FAN9 Positon
#pin: PD15
#max_power: 1
#shutdown_speed: 0
#kick_start_time: 0.1
#off_below: 0.10

#[fan_generic RSCS]
##  RSCS Fans - In FAN1 Positon
#pin: PA1
#max_power: 1
#shutdown_speed: 0
#kick_start_time: 0.1
#off_below: 0.10

#[controller_fan driver_fan] 
# This is if you connect your driver fan to Super8 
#or if you want to add fan to the Super8. Other wise connect them in the driver fan ports
#stepper: stepper_x
#pin: PD14
#max_power: 1
#shutdown_speed: 0
#kick_start_time: 0.1
#off_below: 0.10

########################
########################

#[temperature_sensor chamber]  optional for chamber temp
#sensor_type: NTC 100K MGB18-104F39050L32
#pullup_resistor: 4700
#sensor_pin: PF5
#min_temp: 0
#max_temp: 60
#gcode_id: C: C

#[temperature_sensor Bed_Edge]
#Sensor_type: Generic 3950
#sensor_pin:PF4

###########################################
#########Custom PINs Definition ############
###########################################

#[output_pin LED]
#In FAN8 position if 12 or 5V
#When 24V use a heater pin like Heat4 PF6
#pin: PF6
#pwm: false
#value: 1
#shutdown_value:1
### gcode command: SET_PIN PIN=LED value=0 to 1

[idle_timeout]
timeout: 1800
gcode =
  {% if printer.pause_resume.is_paused %}
    M104 S0
  {% else %}
    TURN_OFF_HEATERS
    #M84
  {% endif %}

################################################################################################
##                                        Probe                                               ##
################################################################################################

#[bed_screws]
#screw1: 
#screw2: 
#screw3: 
#screw4: 

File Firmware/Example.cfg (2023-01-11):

###### Board: Super 8 v1.2 ###
######  AWD  #################


[include mainsail.cfg]
[include timelapse.cfg]

##### Vz235############
#######################

[printer]
kinematics: corexy
max_velocity: 2500
max_accel: 50000
max_accel_to_decel: 50000
max_z_velocity: 20
max_z_accel: 1000
square_corner_velocity: 10

########################
########################


[mcu]
serial:/dev/serial/by-id/usb-Klipper_stm32f407xx_3D0038000947393436343431-if00
#restart_method: command

[mcu rpi]
serial: /tmp/klipper_host_mcu

[adxl345]
cs_pin: rpi:None

[resonance_tester]
accel_chip: adxl345
probe_points:
    117,117,20  # an example

########################
########################


[stepper_x]
##	in M4 position
step_pin: PE15
dir_pin: !PE11
enable_pin: !PF2
rotation_distance: 40
microsteps: 16
full_steps_per_rotation: 200  
endstop_pin: ^PG11
position_endstop: 0
position_max: 150
homing_speed: 25  
homing_retract_dist: 0
[tmc5160 stepper_x] 
spi_bus: spi3 
cs_pin: PE10
interpolate: false 
run_current: 1.75
sense_resistor: 0.033
#spi_speed: 1000000
stealthchop_threshold: 0
#driver_IHOLDDELAY: 6
#driver_TPOWERDOWN: 10
#driver_TBL: 2
#driver_TOFF: 4
#driver_HEND: 5
#driver_HSTRT: 0
#driver_tpfd: 0
#driver_pwm_autoscale: True
#driver_pwm_autograd: True
#driver_pwm_freq: 2
#driver_PWM_GRAD: 0
#driver_PWM_OFS: 0
#driver_PWM_REG: 0
#driver_PWM_LIM: 0



[stepper_x1]
##	in M6 position
step_pin: PE0
dir_pin: !PG3
enable_pin: !PG4
rotation_distance: 40
microsteps: 16
full_steps_per_rotation: 200  
[tmc5160 stepper_x1] 
spi_bus: spi3
cs_pin: PG2
interpolate: false
run_current: 1.75
sense_resistor: 0.033
#spi_speed: 1000000
stealthchop_threshold: 0







[stepper_y]
##	in M5 position
step_pin: PE1
dir_pin: !PF0
enable_pin: !PC15
rotation_distance: 40
microsteps: 16
full_steps_per_rotation: 200  
endstop_pin: ^PG12
position_endstop: -4
position_min: -4
position_max: 150
homing_speed: 25  
homing_retract_dist: 0
[tmc5160 stepper_y] 
spi_bus: spi3
cs_pin: PF1 
interpolate: false
run_current: 1.75
sense_resistor: 0.033
#spi_speed: 1000000
stealthchop_threshold: 0





[stepper_y1]
##	in M7 position
step_pin: PE6
dir_pin: !PG6
enable_pin: !PG7
rotation_distance: 40
microsteps: 16
full_steps_per_rotation: 200 
[tmc5160 stepper_y1] 
spi_bus: spi3
cs_pin: PG5
interpolate: false
run_current: 1.75
sense_resistor: 0.033
#spi_speed: 1000000
stealthchop_threshold: 0






##########################



[stepper_z]
## In M0 position
step_pin: PE2
dir_pin: !PC5
enable_pin: !PF11
microsteps: 32
rotation_distance: 4
endstop_pin: PG10
position_endstop: 0.0
position_max: 125
full_steps_per_rotation: 200
homing_retract_dist: 5.0
homing_positive_dir: false
homing_speed: 5.0
second_homing_speed: 2.5
step_pulse_duration: 0.000004
[tmc2209 stepper_z]
interpolate: false
uart_pin: PC4
run_current: 1.2
sense_resistor: 0.110
stealthchop_threshold: 0

#########################

[extruder]
##iN M1 position
### Vz-HextrudORT
step_pin: PE3
dir_pin: !PF13
enable_pin: !PF14
microsteps: 16
rotation_distance: 4.55 
nozzle_diameter: 0.5
filament_diameter: 1.750
heater_pin: PB0
sensor_type: ATC Semitec 104NT-4-R025H42G
sensor_pin: PF4
###
control: pid
pid_kp = 22.348
pid_ki = 1.128
pid_kd = 110.536
min_temp: 0
max_temp: 400
full_steps_per_rotation: 200
max_extrude_only_distance: 1000.0
max_extrude_cross_section: 500
max_extrude_only_velocity: 200
max_extrude_only_accel: 10000
min_extrude_temp: 0
pressure_advance: 0.02
pressure_advance_smooth_time: 0.03
[tmc2209 extruder]
interpolate: false
uart_pin: PF12
run_current: 0.85
sense_resistor: 0.110
stealthchop_threshold: 0



########################
########################

[heater_bed]
heater_pin: PE5
sensor_type: Generic 3950
sensor_pin: PC1
control: pid
pid_Kp: 53.395
pid_Ki: 3.296
pid_Kd: 216.251
min_temp: 0
max_temp: 110


########################
#### FANS ##############
########################

[fan]
##	Print Cooling Fan - GPIO26
pin: rpi:gpio26
max_power: 1
cycle_time: 0.002
hardware_pwm: false
shutdown_speed: 0

[heater_fan hotend_fan]
##	Hotend Fan - FAN0 Connector
pin: PA0
max_power: 1.0
kick_start_time: 0.5
heater: extruder
heater_temp: 50.0

[fan_generic Exhaust_fan]
##  exhaust fan - In FAN4
pin: PA15
max_power: 1
shutdown_speed: 0
kick_start_time: 0.1
off_below: 0.10

[fan_generic chamber_fan]
##  chamber fan - In FAN9 Positon
pin: PD15
max_power: 1
shutdown_speed: 0
kick_start_time: 0.1
off_below: 0.10

#[fan_generic RSCS]
##  RSCS Fans - In FAN1 Positon
#pin: PA1
#max_power: 1
#shutdown_speed: 0
#kick_start_time: 0.1
#off_below: 0.10

[controller_fan driver_fan]
stepper: stepper_x
pin: PB11
max_power: 1
shutdown_speed: 0
kick_start_time: 0.1
off_below: 0.10

########################
########################

[temperature_sensor chamber]
sensor_type: NTC 100K MGB18-104F39050L32
pullup_resistor: 4700
sensor_pin: PF9
min_temp: 0
max_temp: 60
gcode_id: C: C


[temperature_sensor raspberry_pi]
sensor_type: temperature_host
min_temp: 10
max_temp: 100



########################
########################

[pause_resume]
recover_velocity: 350

########################
########################

#[filament_switch_sensor sentinel]
#pause_on_runout: true
#switch_pin: PA8
#runout_gcode:
#	G91
#    G1 E-30 F2500
#  	G90
#	G1 X0 Y0 F30000
#  	M104 S0

########################
########################

#[homing_override]
#set_position_z: 0
#axes: xy
#gcode:
# G0 Z3 F200
# G28 y0 
# G28 x0
# G28 Z0

########################
########################

[firmware_retraction]
retract_length: 0.6
retract_speed: 50
unretract_extra_length: 0
unretract_speed: 50

###########################################
#########Custom PINs Definition ############
###########################################


[output_pin LED]
#In FAN8 position
pin: PD14
pwm: false
value: 1
shutdown_value:1



[output_pin BackLED]
#In FAN9 position
pin: PD12
pwm: false
value: 1
shutdown_value:1




################################################################################################
################################################################################################
#####				MACROS	
##################

[gcode_macro ACCELL_TEST_X]
gcode:

    {% set steps = params.STEPS|default(100)|int %}
    {% set speed = params.VELOCITY|default(1000)|float * 60 %}

    {% set inset = 10.0|float %}
    {% set accel = 30000|int %}
    {% set maxX = printer.configfile.settings.stepper_x.position_max|float - inset %}
    {% set maxY = printer.configfile.settings.stepper_y.position_max|float - inset %}
    {% set minX = printer.configfile.settings.stepper_x.position_min|float + inset %}
    {% set minY = printer.configfile.settings.stepper_y.position_min|float + inset %}

    SAVE_GCODE_STATE NAME=accelltest_state

    SET_VELOCITY_LIMIT ACCEL={accel} 
    SET_VELOCITY_LIMIT ACCEL_TO_DECEL={accel}
    G28
	G1 Z5
    G1 X{minX} Y{minY} F{speed} 

    {% for INTERVAL in range(steps) %}
        {% set eff = accel + (INTERVAL * 1000) %} 
        SET_VELOCITY_LIMIT ACCEL={eff} 
        SET_VELOCITY_LIMIT ACCEL_TO_DECEL={eff}
        G1 X{minX} Y{minY} F{speed}  
        G1 X{maxX} Y{maxY} F{speed}  

    {% endfor %}    

    RESTORE_GCODE_STATE NAME=accelltest_state 
	
	
	
[gcode_macro ACCELL_TEST_Y]
gcode:

    {% set steps = params.STEPS|default(100)|int %}
    {% set speed = params.VELOCITY|default(1000)|float * 60 %}

    {% set inset = 10.0|float %}
    {% set accel = 10000|int %}
    {% set maxX = printer.configfile.settings.stepper_x.position_max|float - inset %}
    {% set maxY = printer.configfile.settings.stepper_y.position_max|float - inset %}
    {% set minX = printer.configfile.settings.stepper_x.position_min|float + inset %}
    {% set minY = printer.configfile.settings.stepper_y.position_min|float + inset %}

    SAVE_GCODE_STATE NAME=accelltest_state

    SET_VELOCITY_LIMIT ACCEL={accel} 
    SET_VELOCITY_LIMIT ACCEL_TO_DECEL={accel}
    G28
	G1 Z5
    G1 X{minX} Y{minY} F{speed} 

    {% for INTERVAL in range(steps) %}
        {% set eff = accel + (INTERVAL * 1000) %} 
        SET_VELOCITY_LIMIT ACCEL={eff} 
        SET_VELOCITY_LIMIT ACCEL_TO_DECEL={eff}
        G1 X{maxX} Y{minY} F{speed}  
        G1 X{minX} Y{maxY} F{speed}  

    {% endfor %}    

    RESTORE_GCODE_STATE NAME=accelltest_state 



[gcode_macro RETRACTION_UP]
gcode:
    {% set CRLEN = printer.firmware_retraction.retract_length|float %}
    {% set NRLEN = CRLEN|float + 0.1 %}
    { action_respond_info("current retract_length %.2f, new retract_length %.2f" % (CRLEN, NRLEN))  }
    SET_RETRACTION RETRACT_LENGTH={NRLEN}    

[gcode_macro RETRACTION_DOWN]
gcode:
    {% set CRLEN = printer.firmware_retraction.retract_length|float %}
    {% set NRLEN = CRLEN|float - 0.1 %}
    { action_respond_info("current retract_length %.2f, new retract_length %.2f" % (CRLEN, NRLEN))  }
    SET_RETRACTION RETRACT_LENGTH={NRLEN}   


#[gcode_macro SET_RETRACTIONLENGTH]
#gcode:
#  SET_RETRACTION RETRACT_LENGTH={params.LENGTH|float}
#  GET_RETRACTION
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

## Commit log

2023-01-15 Update CAD
2023-01-30 CAD update
    [X_Stopblock.stl, Y_Stopblock.stl]
2023-02-22 Uploaded Doorknob Files.
    [Insert_x2.stl, Knob_x2.stl, Left_Latch_Body.stl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]
2023-02-24 update CAD.
2023-03-28 Adding Y alu gantry STLs and bom for both printed and alu
    [1.4mm M5 spacer.stl, 11mm M5 spacer.stl, Gantry Bottom.stl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]
2023-03-28 adding wiring diagram
2023-03-29 Adding Y gantry MGN9C adapter
    [MGN9C Adapter.step, MGN9C Adapter.stl]
2023-05-08 Updated Z
    Changed Linear bearings from LM10UU to LM10U and changed Oldham Mount to sit 10mm higher to also give more Z space.
2023-05-10 adding Mellow-Fly LCD enclosure
    [Back cover.stl, Front Screen Cover.stl, Front cover.stl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]
2023-05-29 Update Front cover.stl
    [Front cover.stl]
2023-06-12 Update AWD MELLOW FLY SUPER 8 WITH CPAP.png
    -changed CPAP wiring to PF8 pin on super8
    -Added ground to SSR heater for those who dont use DIN rail
    -Added thermal fuse to bed for those who don't use Mellow bed heater with built-in thermal fuse
2023-06-12 firmware files updated
    -Printer.cfg updated to have CPAP pin on PF8 on super8
    -firmware bin file updated to have pin PF8 disabled at boot up or when klipper is not running
    [150AWD-printer.cfg]
2023-07-15 adding mellow fly LCD mount cad
    [Screen enclosure.step]
2023-07-15 adding Mellow fly screen mount cad
    [Back cover.stl, Front cover.stl]
2023-07-17 update to Mellow Fly 5" screen enclosure (front only)
    [Front cover.stl]
2023-08-03 Single Z piece.
    [2x_Z_One_Piece.stl, Bed Alligment Tool V2.stl, Lead screw support.stl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]
2023-08-20 Update 150AWD-printer.cfg
    same as docs.
    [150AWD-printer.cfg]
2023-08-20 update wiring diagram.
2023-08-21 upload Macro files.
    [150AWD-printer.cfg, Exclude_Object.cfg, Macro.cfg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]
2024-02-11 Updated MGN mounts
    updated the MGN printed MGN mounts for the new CNC X Beam with 21mm spacing.
    [Y_gantry_Left_bottom.stl, Y_gantry_Left_top.stl, Y_gantry_Right_bottom.stl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]
